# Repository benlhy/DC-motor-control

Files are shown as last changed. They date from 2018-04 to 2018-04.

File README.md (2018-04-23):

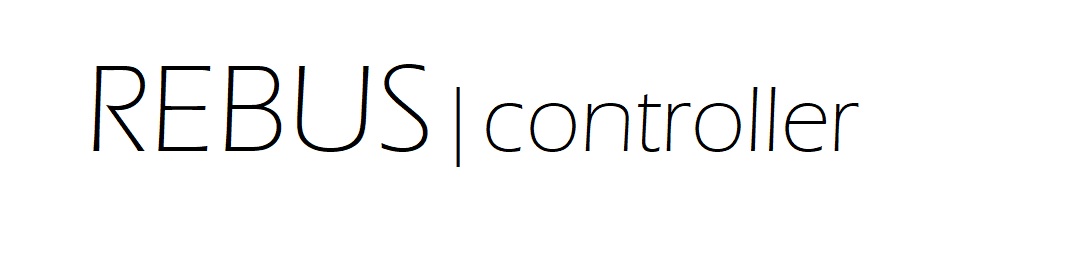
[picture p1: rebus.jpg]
rebus


This a DC motor controller built around the TI TIVA TM4C123 chip. It has position and velocity control and can be linked up to form a multi-axis system. 

# Layouts

Layout for the standalone board is here:

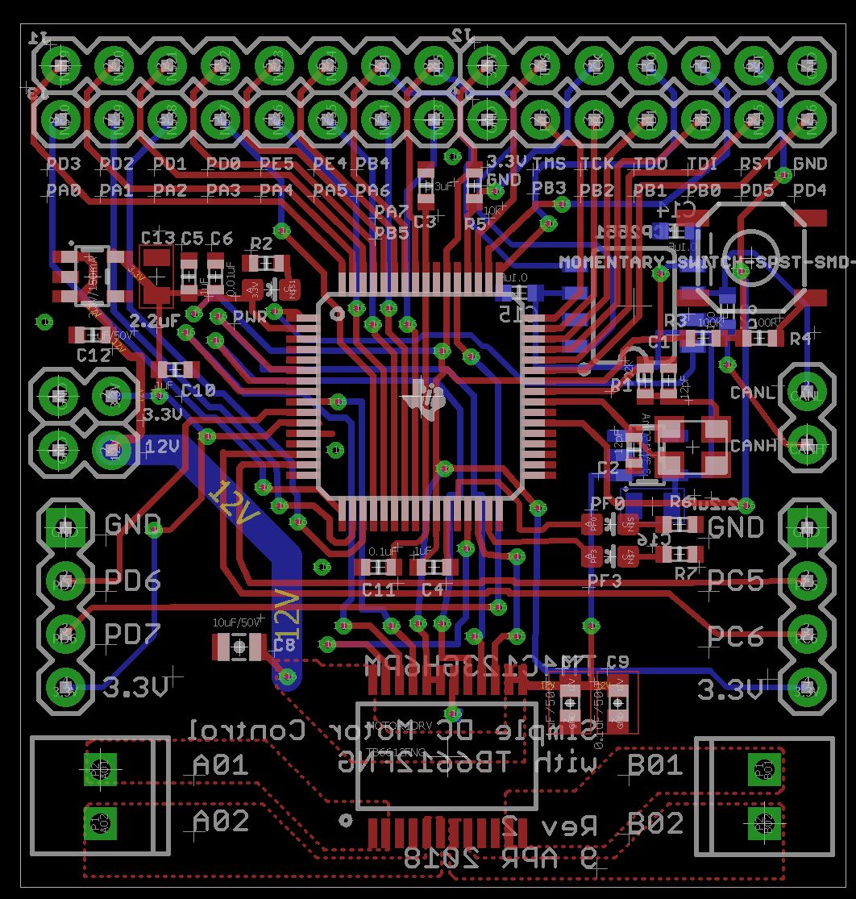
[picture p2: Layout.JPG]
layout


Boost board layout:

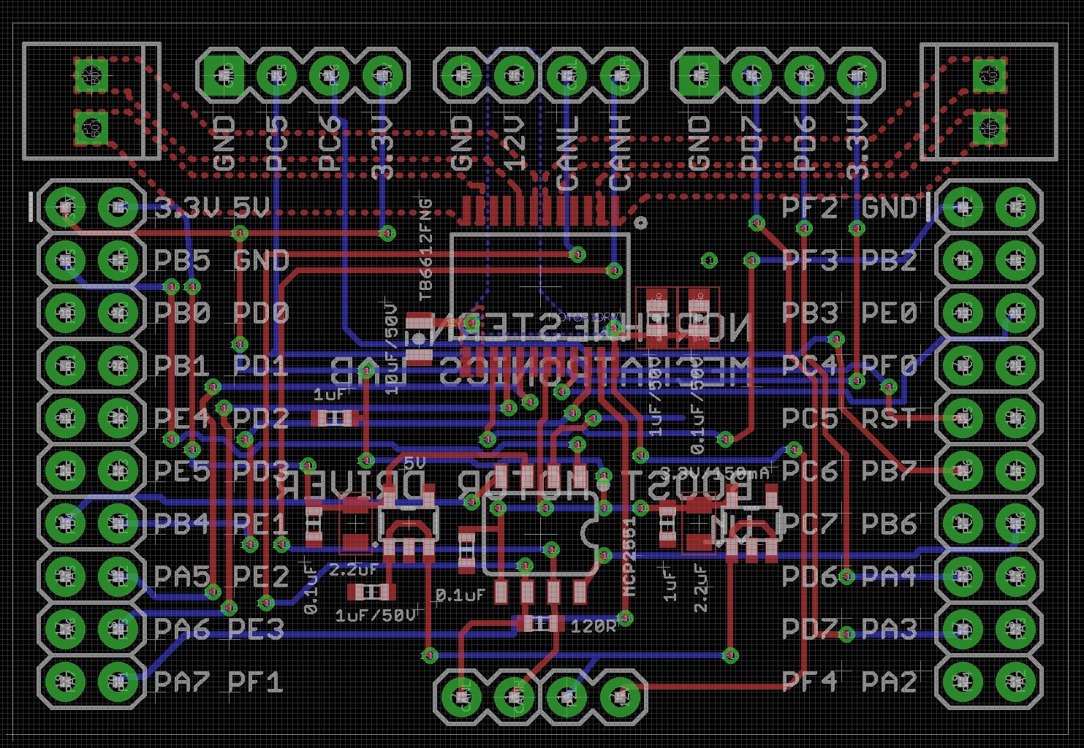
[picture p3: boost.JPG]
boost


# Programming

To program this board you will need Launchpad that has the programming pins broken out. Please see the [programming repo](https://github.com/benlhy/DC-Control-Module) for more details.

# Design Decisions

## Motor Driver
TB6612FNG - 2.5 ~ 13.5V, 1.3A per channel, max 3.2A
DRV8848 - 4 ~ 18V, 1A per channel, max 2A

## Regulator
MIC5219 - 20V input range, and comes in 5V flavour and 3.3V flavour

## Crystal
NDK (NX3325SA) was chosen because guidelines indicated that Max DI(uW) > 200, and most of Abracon's crystals had a max DI of 100. Anything with CL greater than 18uF was also not acceptable. From Table 30-24, the recommended component values were 12pF for the capacitors and Rs of 2k. This was the smallest crystal that was recommended. Note that it is NX3225GA that was recommended, but the difference appears to be ordering information.

## Reset
A 100R resistor is placed in series with the reset switch to prevent ringing as suggested in the design guide.

# References
1. http://www.ti.com/lit/ds/symlink/tm4c123gh6pm.pdf
2. http://www.ti.com/lit/an/spma059/spma059.pdf

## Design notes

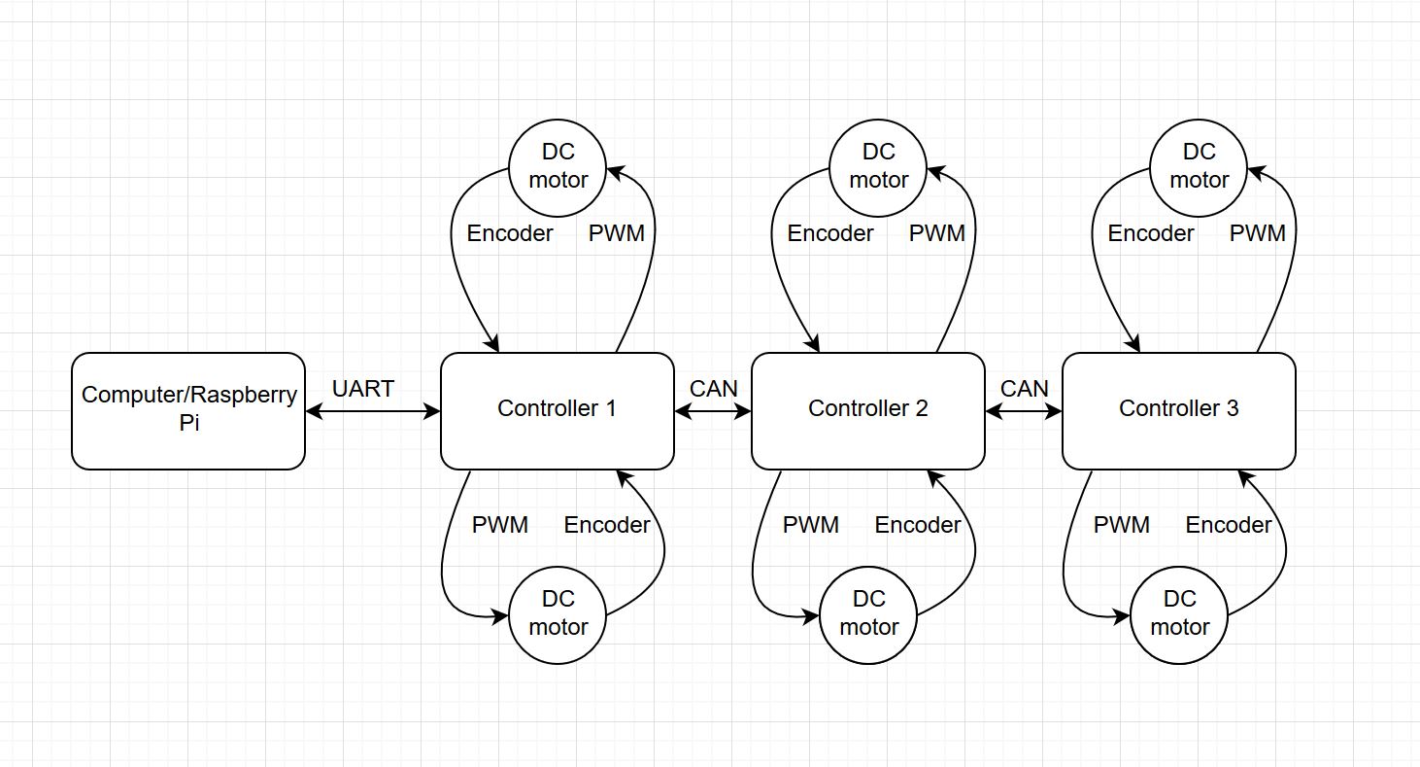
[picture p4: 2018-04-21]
diagram.JPG

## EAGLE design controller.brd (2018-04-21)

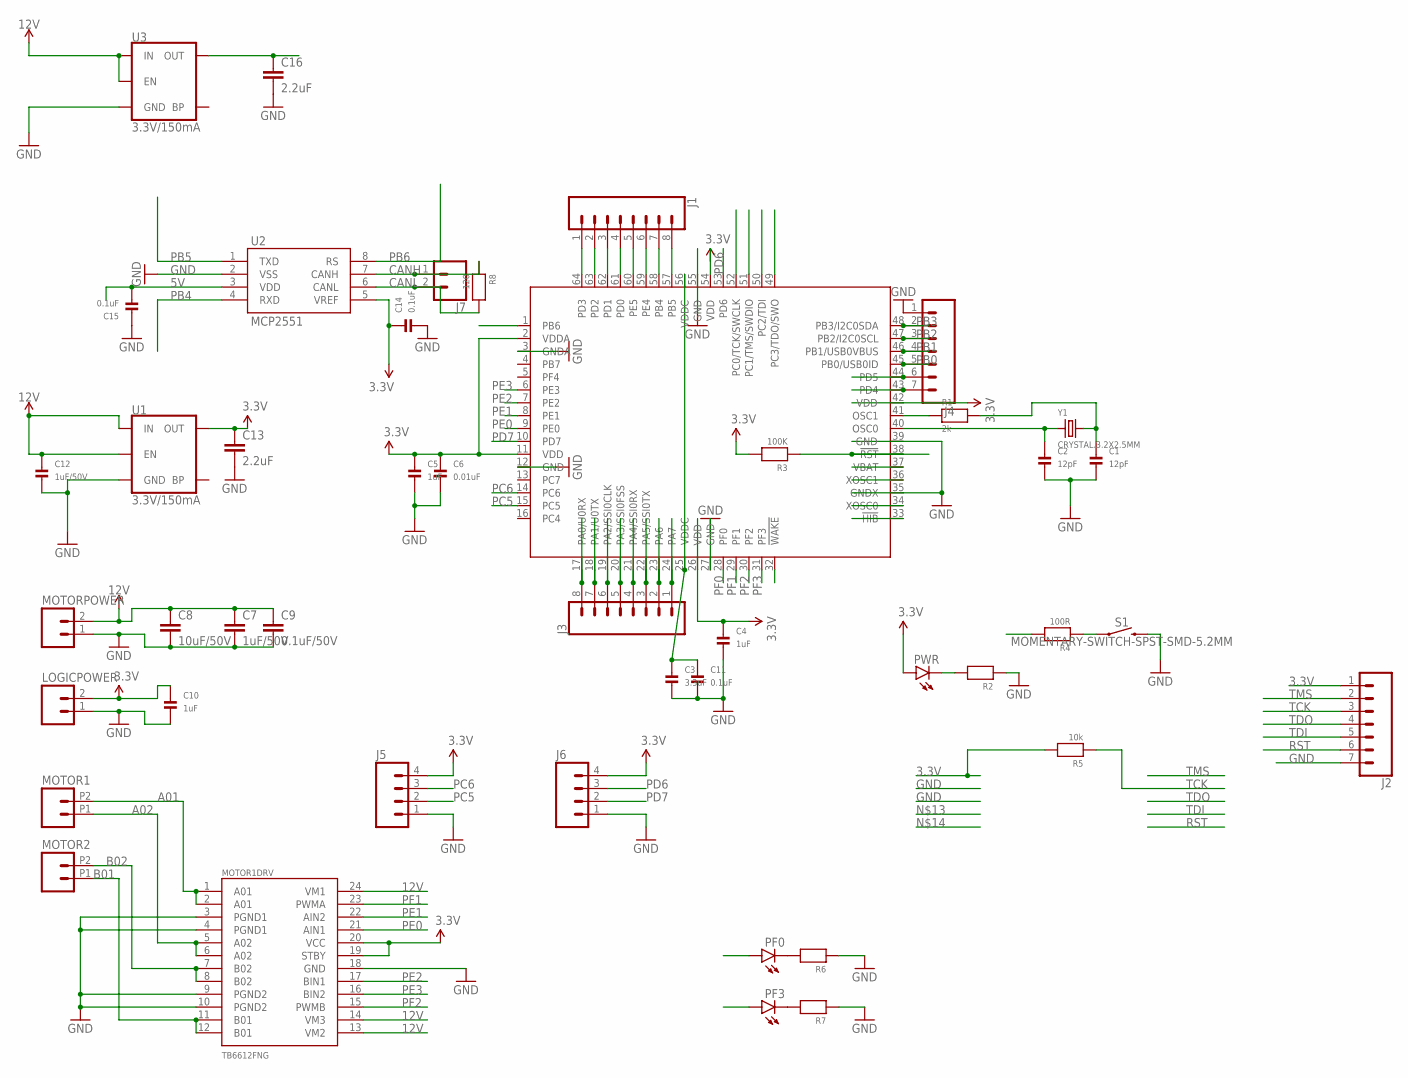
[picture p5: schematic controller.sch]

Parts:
C1, C2: 12pF; _0603MP
C3: 3.3uF; _0603MP
C4, C5, C10: 1uF; _0603MP
C6: 0.01uF; _0603MP
C7: 1uF/50V; 0603-CAP
C8: 10uF/50V; 0805-CAP
C9: 0.1uF/50V; 0603-CAP
C11, C14, C15: 0.1uF; _0603MP
C12: 1uF/50V; _0603MP
C13, C16: 2.2uF; 0805
IC1: TM4C123[7,G]XXPM; PM_S-PQFP-G64
J1, J3: CONN_08"; 1X08@1
J2: CONN_07; 1X07@1
J4: M07; 1X07
J5, J6: M04PTH; 1X04
J7: CONN_02; 1X02
LOGICPOWER: M02PTH; 1X02@1
MOTOR1, MOTOR2: M022.54MM_SCREWTERM; 1X02_2.54_SCREWTERM@1
MOTOR1DRV: TB6612FNG; SSOP24
MOTORPOWER: M02PTH; 1X02@1
PF0, PF3: LED0603; LED-0603
PWR: LED0603; LED-0603
R1: 2k; _0603MP
R2, R6, R7: RESISTOR_0603MP; _0603MP
R3: 100K; _0603MP
R4: 100R; _0603MP
R5: 10k; _0603MP
R8: 120; _0603MP
S1: MOMENTARY-SWITCH-SPST-SMD-5.2MM; TACTILE_SWITCH_SMD_5.2MM
U1, U3: 3.3V/150mA; SOT23-5
U2: MCP2551; SO08
Y1: CRYSTAL.3.2X2.5MM; 3.2X2.5MM

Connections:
3.3V: C4.1, C5.1, C6.1, C10.1, C13.1, C14.1, IC1.2 (VDDA), IC1.11 (VDD), IC1.26 (VDD), IC1.42 (VDD), IC1.54 (VDD), J2.1, J5.4, J6.4, LOGICPOWER.2, MOTOR1DRV.19 (STBY), MOTOR1DRV.20 (VCC), PWR.A, R3.2, R5.2, U1.5 (OUT), U2.5 (VREF)
5V: C15.2, C16.1, U2.3 (VDD), U3.5 (OUT)
12V: C7.1, C8.1, C9.1, C12.1, MOTOR1DRV.13 (VM2), MOTOR1DRV.14 (VM3), MOTOR1DRV.24 (VM1), MOTORPOWER.2, U1.1 (IN), U1.3 (EN), U3.1 (IN), U3.3 (EN)
A01: MOTOR1.P2 (2), MOTOR1DRV.1 (A01), MOTOR1DRV.2 (A01)
A02: MOTOR1.P1 (1), MOTOR1DRV.5 (A02), MOTOR1DRV.6 (A02)
B01: MOTOR1DRV.11 (B01), MOTOR1DRV.12 (B01), MOTOR2.P1 (1)
B02: MOTOR1DRV.7 (B02), MOTOR1DRV.8 (B02), MOTOR2.P2 (2)
CANH: J7.1, R8.1, U2.7 (CANH)
CANL: J7.2, R8.2, U2.6 (CANL)
GND: C1.2, C2.2, C3.2, C4.2, C5.2, C6.2, C7.2, C8.2, C9.2, C10.2, C11.2, C12.2, C13.2, C14.2, C15.1, C16.2, IC1.3 (GNDA), IC1.12 (GND), IC1.27 (GND), IC1.35 (GNDX), IC1.39 (GND), IC1.55 (GND), J2.7, J4.1, J5.1, J6.1, LOGICPOWER.1, MOTOR1DRV.3 (PGND1), MOTOR1DRV.4 (PGND1), MOTOR1DRV.9 (PGND2), MOTOR1DRV.10 (PGND2), MOTOR1DRV.18 (GND), MOTORPOWER.1, R2.1, R6.1, R7.1, S1.3 (2), U1.2 (GND), U2.2 (VSS), U3.2 (GND)
unnamed: IC1.41 (OSC1), R1.1
unnamed: C2.1, IC1.40 (OSC0), Y1.1
unnamed: C3.1, C11.1, IC1.25 (VDDC), IC1.56 (VDDC)
unnamed: C1.1, R1.2, Y1.3 (2)
unnamed: PF0.C, R6.2
unnamed: PF3.C, R7.2
unnamed: IC1.64 (PD3), J1.1
unnamed: IC1.63 (PD2), J1.2
unnamed: IC1.62 (PD1), J1.3
unnamed: IC1.61 (PD0), J1.4
unnamed: IC1.60 (PE5), J1.5
unnamed: IC1.59 (PE4), J1.6
unnamed: IC1.24 (PA7), J3.1
unnamed: IC1.23 (PA6), J3.2
unnamed: IC1.22 (PA5/SSI0TX), J3.3
unnamed: IC1.21 (PA4/SSI0RX), J3.4
unnamed: IC1.20 (PA3/SSI0FSS), J3.5
unnamed: IC1.19 (PA2/SSI0CLK), J3.6
unnamed: IC1.18 (PA1/U0TX), J3.7
unnamed: IC1.17 (PA0/U0RX), J3.8
unnamed: IC1.44 (PD5), J4.6
unnamed: IC1.43 (PD4), J4.7
unnamed: PWR.C, R2.2
unnamed: R4.1, S1.1
PB0: IC1.45 (PB0/USB0ID), J4.5
PB1: IC1.46 (PB1/USB0VBUS), J4.4
PB2: IC1.47 (PB2/I2C0SCL), J4.3
PB3: IC1.48 (PB3/I2C0SDA), J4.2
PB4: IC1.58 (PB4), J1.7, U2.4 (RXD)
PB5: IC1.57 (PB5), J1.8, U2.1 (TXD)
PB6: IC1.1 (PB6), U2.8 (RS)
PC5: IC1.15 (PC5), J5.2
PC6: IC1.14 (PC6), J5.3
PD6: IC1.53 (PD6), J6.3
PD7: IC1.10 (PD7), J6.2
PE0: IC1.9 (PE0), MOTOR1DRV.21 (AIN1)
PE1: IC1.8 (PE1), MOTOR1DRV.22 (AIN2)
PE2: IC1.7 (PE2), MOTOR1DRV.17 (BIN1)
PE3: IC1.6 (PE3), MOTOR1DRV.16 (BIN2)
PF0: IC1.28 (PF0), PF0.A
PF1: IC1.29 (PF1), MOTOR1DRV.23 (PWMA)
PF2: IC1.30 (PF2), MOTOR1DRV.15 (PWMB)
PF3: IC1.31 (PF3), PF3.A
RST: IC1.38 (!RST), J2.6, R3.1, R4.2
TCK: IC1.52 (PC0/TCK/SWCLK), J2.3, R5.1
TDI: IC1.50 (PC2/TDI), J2.5
TDO: IC1.49 (PC3/TDO/SWO), J2.4
TMS: IC1.51 (PC1/TMS/SWDIO), J2.2

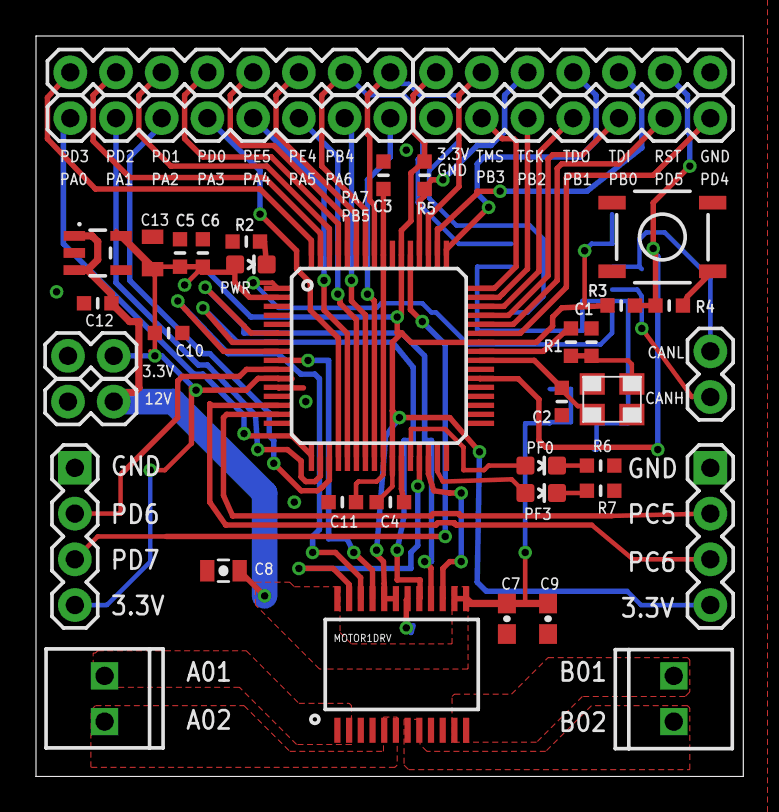
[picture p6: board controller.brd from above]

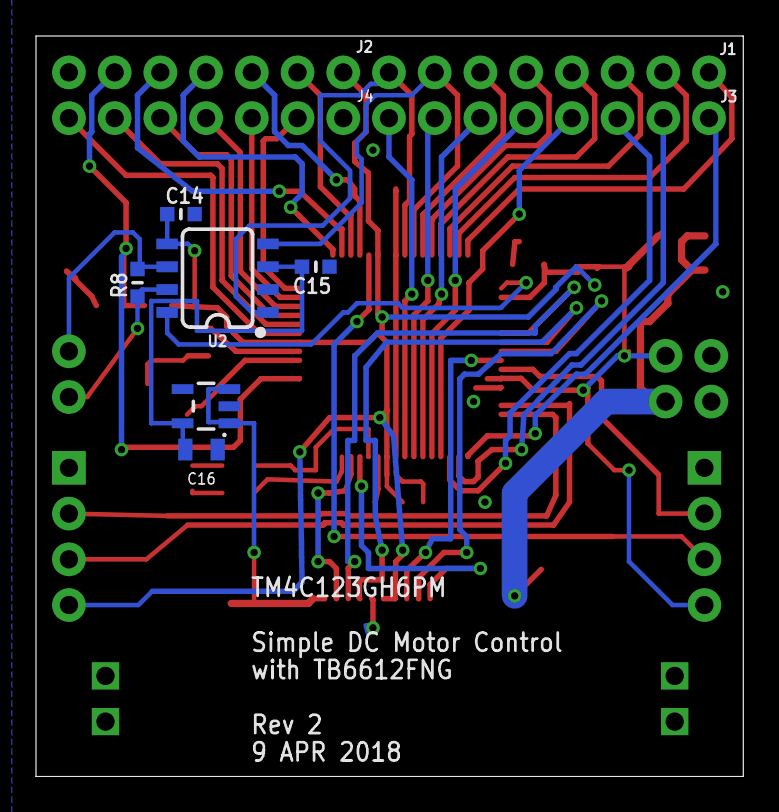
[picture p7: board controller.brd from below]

Board: 2 copper layers, 39.3 x 41.1 mm, 45 parts (6 on the bottom side), 58 nets.

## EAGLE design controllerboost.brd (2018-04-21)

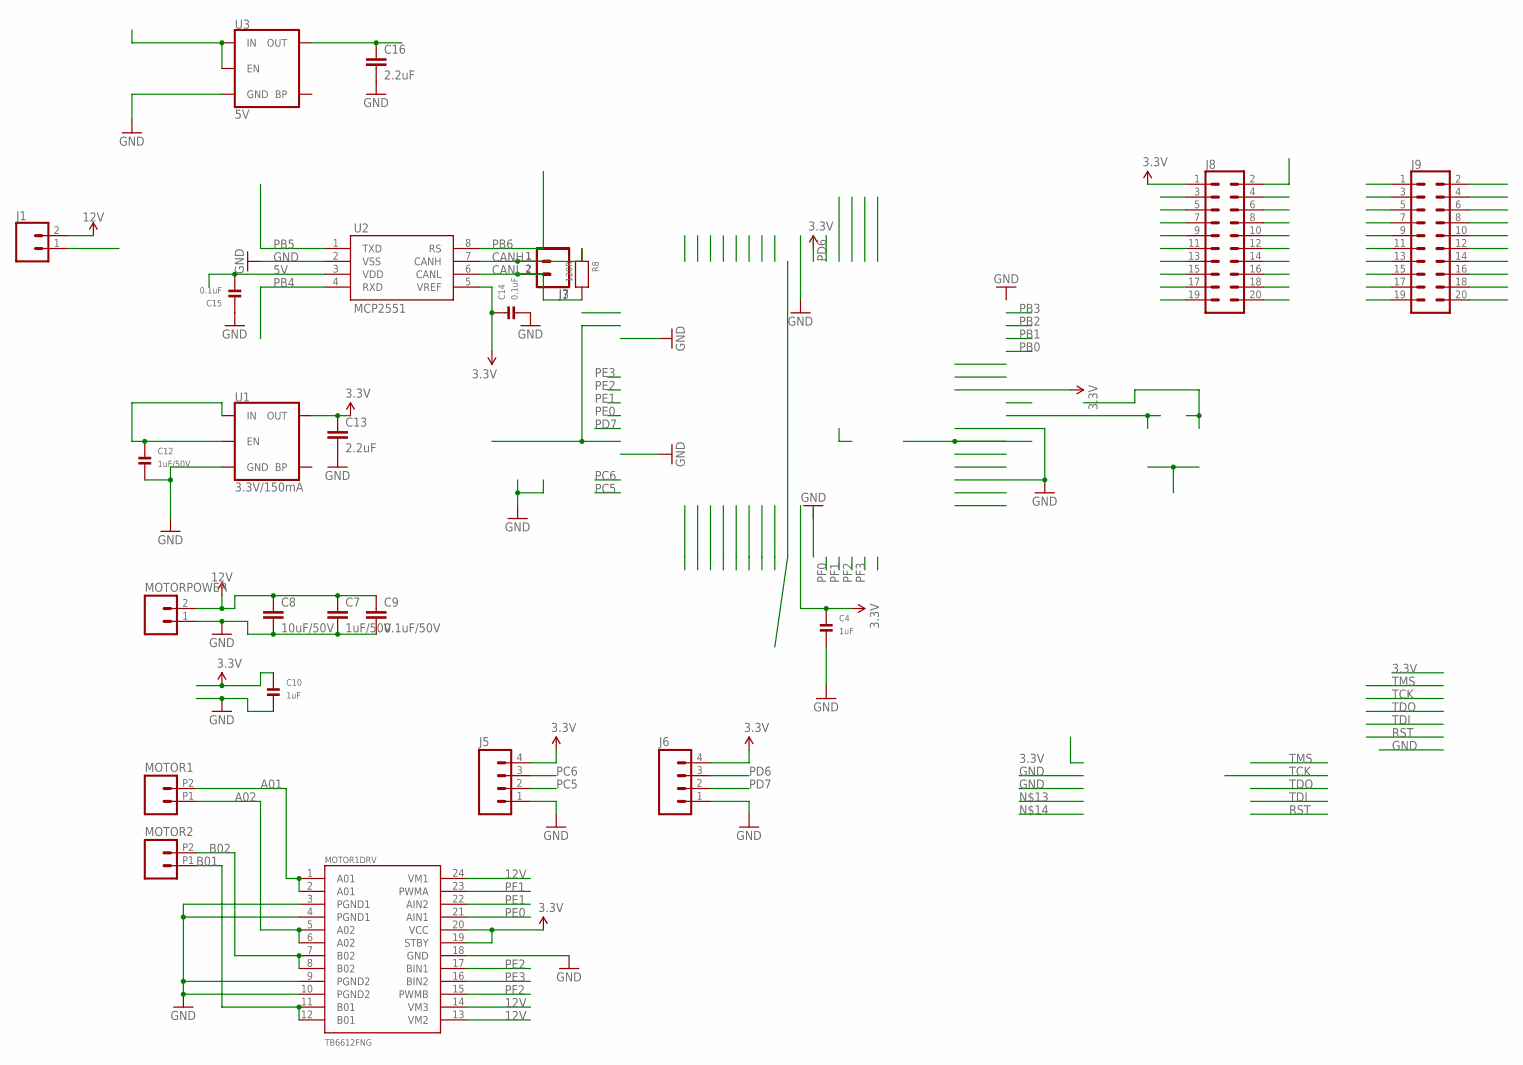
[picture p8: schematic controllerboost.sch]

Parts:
C4, C10: 1uF; _0603MP
C7: 1uF/50V; 0603-CAP
C8: 10uF/50V; 0805-CAP
C9: 0.1uF/50V; 0603-CAP
C12: 1uF/50V; _0603MP
C13, C16: 2.2uF; 0805
C14, C15: 0.1uF; _0603MP
J1, J3, J7: CONN_02; 1X02
J5, J6: M04PTH; 1X04
J8, J9: CONN_10X2; 2X10
MOTOR1, MOTOR2: M022.54MM_SCREWTERM; 1X02_2.54_SCREWTERM@1
MOTOR1DRV: TB6612FNG; SSOP24
MOTORPOWER: M02PTH; 1X02@1
R8: 120R; _0603MP
U1: 3.3V/150mA; SOT23-5
U2: MCP2551; SO08
U3: 5V; SOT23-5

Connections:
3.3V: C4.1, C10.1, C13.1, C14.1, J5.4, J6.4, J8.1, MOTOR1DRV.19 (STBY), MOTOR1DRV.20 (VCC), U1.5 (OUT), U2.5 (VREF)
5V: C15.2, C16.1, J8.2, U2.3 (VDD), U3.5 (OUT)
12V: C7.1, C8.1, C9.1, J1.2, MOTOR1DRV.13 (VM2), MOTOR1DRV.14 (VM3), MOTOR1DRV.24 (VM1), MOTORPOWER.2
A01: MOTOR1.P2 (2), MOTOR1DRV.1 (A01), MOTOR1DRV.2 (A01)
A02: MOTOR1.P1 (1), MOTOR1DRV.5 (A02), MOTOR1DRV.6 (A02)
B01: MOTOR1DRV.11 (B01), MOTOR1DRV.12 (B01), MOTOR2.P1 (1)
B02: MOTOR1DRV.7 (B02), MOTOR1DRV.8 (B02), MOTOR2.P2 (2)
CANH: J3.1, J7.1, R8.1, U2.7 (CANH)
CANL: J3.2, J7.2, R8.2, U2.6 (CANL)
GND: C4.2, C7.2, C8.2, C9.2, C10.2, C12.2, C13.2, C14.2, C15.1, C16.2, J5.1, J6.1, J8.4, J9.2, MOTOR1DRV.3 (PGND1), MOTOR1DRV.4 (PGND1), MOTOR1DRV.9 (PGND2), MOTOR1DRV.10 (PGND2), MOTOR1DRV.18 (GND), MOTORPOWER.1, U1.2 (GND), U2.2 (VSS), U3.2 (GND)
P2L: C12.1, J1.1, U1.1 (IN), U1.3 (EN), U3.1 (IN), U3.3 (EN)
PA2: J9.20
PA3: J9.18
PA4: J9.16
PA5: J8.15
PA6: J8.17
PA7: J8.19
PB0: J8.5
PB1: J8.7
PB2: J9.4
PB3: J9.5
PB4: J8.13, U2.4 (RXD)
PB5: J8.3, U2.1 (TXD)
PB6: J9.14, U2.8 (RS)
PB7: J9.12
PC4: J9.7
PC5: J5.2, J9.9
PC6: J5.3, J9.11
PC7: J9.13
PD0: J8.6
PD1: J8.8
PD2: J8.10
PD3: J8.12
PD6: J6.3, J9.15
PD7: J6.2, J9.17
PE0: J9.6, MOTOR1DRV.21 (AIN1)
PE1: J8.14, MOTOR1DRV.22 (AIN2)
PE2: J8.16, MOTOR1DRV.17 (BIN1)
PE3: J8.18, MOTOR1DRV.16 (BIN2)
PE4: J8.9
PE5: J8.11
PF0: J9.8
PF1: J8.20, MOTOR1DRV.23 (PWMA)
PF2: J9.1, MOTOR1DRV.15 (PWMB)
PF3: J9.3
PF4: J9.19
RST: J9.10

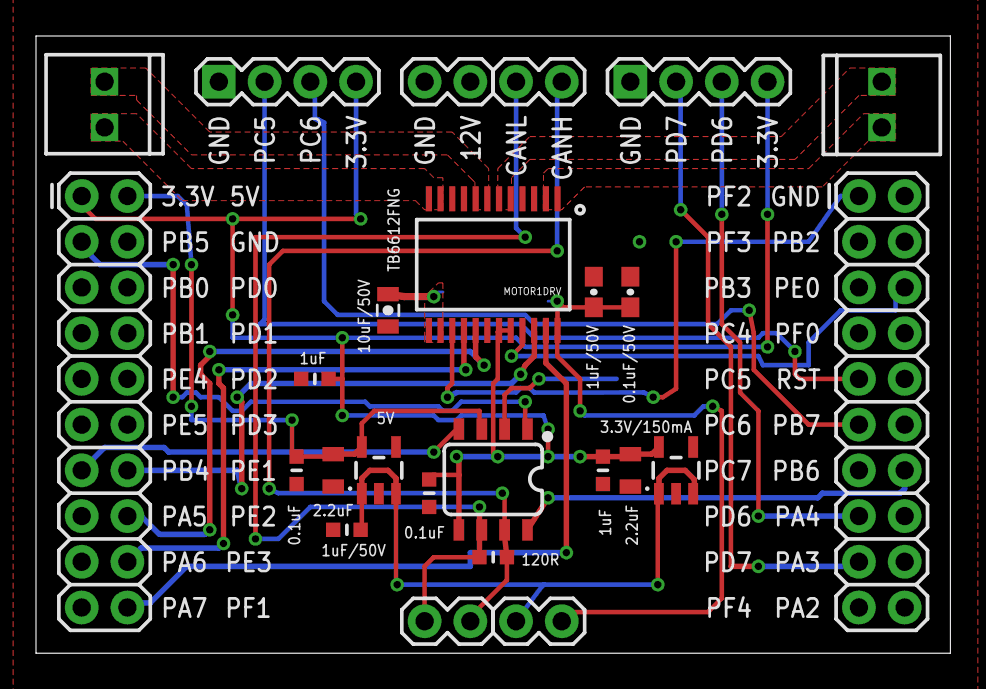
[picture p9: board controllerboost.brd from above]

Board: 2 copper layers, 50.8 x 34.3 mm, 25 parts (0 on the bottom side), 24 nets.

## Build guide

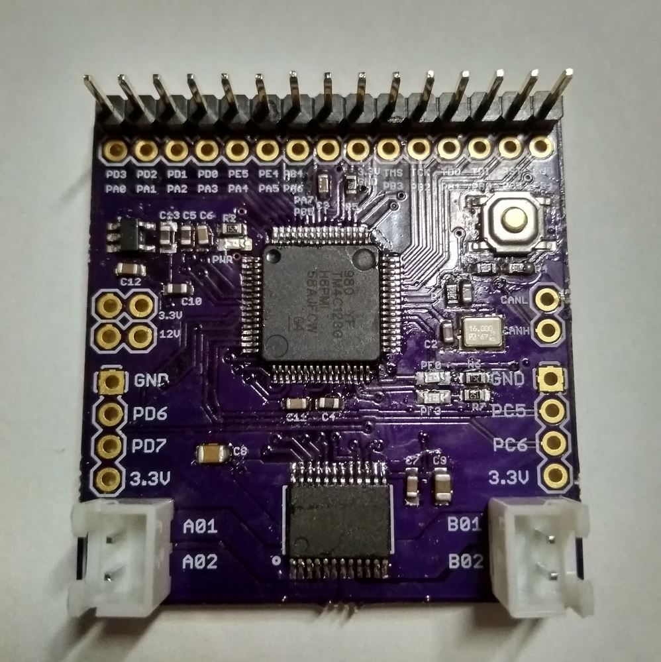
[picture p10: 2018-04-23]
solderedBoard.JPG

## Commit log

2018-04-08 Updated board, added onboard 3.3V power, changed crystal size
    [controller.brd, controller.sch]
2018-04-11 Wired it up
    [firely.brd, firely.sch]
2018-04-21 cleaned and updated files
    [controller.brd, controller.sch, controllerboost.brd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]

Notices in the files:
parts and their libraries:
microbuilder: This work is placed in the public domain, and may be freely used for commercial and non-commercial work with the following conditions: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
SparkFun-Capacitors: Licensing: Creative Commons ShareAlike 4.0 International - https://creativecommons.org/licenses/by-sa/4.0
